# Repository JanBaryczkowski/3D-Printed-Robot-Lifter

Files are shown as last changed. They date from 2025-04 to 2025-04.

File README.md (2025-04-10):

Description: 
The lifter’s purpose is to enable the device to reach higher than the arm itself allows. Consequently, the robot operates within a broader workspace without increasing its size or modifying the arm’s construction.
The project comprises strength calculations, a 3D model of the lifter assembled with carefully selected parts and subassemblies, as well as technical drawings that predominantly consist of assembly views and a few component details. 
It also serves as part of the project assignments from the Fundamentals of Machine Construction course. The work not only demonstrates rigorous analytical and design skills but also highlights a practical approach to solving engineering
challenges while ensuring optimal functionality and structural integrity.

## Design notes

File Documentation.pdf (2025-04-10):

# Podstawy Konstrukcji Maszyn

# Projekt Podnośnika do ramienia robota wydrukowanego w 3D

## Jan Baryczkowski 152159 Mechatronika sem. V Grupa MCH1

1. Przegląd stanu techniki Podnośnik ten służy do automatycznego transportowania ramienia robota wydrukowanego w 3D wraz z przenoszonymi przez nie elementami w celu poszerzenia zakresu działania robota bez konieczności zwiększenia rozmiarów lub rozbudowy konstrukcji samego robota. Budowa tego mechanizmu nie ma zastosowania w przemyśle ze względu na małe rozmiary samego robota, ale mogłaby posłużyć jako jeden z wielu elementów Smart Home w celu np segregacji małych obiektów na różnych wysokościach za pomocą samego podnośnika wraz z

robotem.

## 2. Schemat kinematyczny

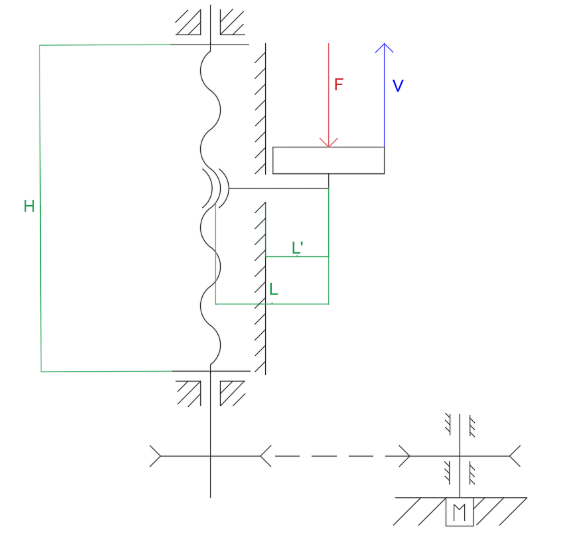
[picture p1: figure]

## 3. Dane wejściowe

## H = 400 mm - długość skoku śruby L = 45 mm- długość ramienia siły do osi śruby F = 10N - siła docisku spowodowana przez masę robota wraz z elementem przez niego przenoszonym V = 0,05 m/s - prędkość posuwu podnośnika

## 4. Spis elementów

L.p. | Nazwa | Szt. | Numer / Norma | Materiał | Uwagi
1 | Śruba trapezowa Tr 10x2 | 1 | MCH-1.00.01.0 | S215 | -
2 | Wał czynny | 1 | MCH-1.00.02.0 | C45 | -
3 | Wał bierny | 1 | MCH-1.00.03.0 | C45 | -
4 | Nakrętka trapezowa Tr 10x2 | 1 | MCH-1.00.04.0 | Brąz Bk331 | -
5 | Korpus - ściana boczna długa | 2 | MCH-1.00.05.0 | PA | -
6 | Korpus - ściana boczna krótka | 2 | MCH-1.00.06.0 | PA | -
7 | Korpus - podstawa dolna | 1 | MCH-1.00.07.0 | PA | -
8 | Korpus - podstawa górna | 1 | MCH-1.00.08.0 | PA | -
9 | Nóżka L - podstawa | 4 | MCH-1.00.09.0 | PA | -
10 | Nóżka H - podstawa | 6 | MCH-1.00.10.0 | PA | -
11 | Noga L - długa | 4 | MCH-1.00.11.0 | PA | -
12 | Noga H - długa | 6 | MCH-1.00.12.0 | PA | -
13 | Noga L - krótka | 3 | MCH-1.00.13.0 | PA | -
14 | Noga H - krótka | 4 | MCH-1.00.14.0 | PA | -
15 | Oprawa łożyska 1 | 2 | MCH-1.00.15.0 | PA | -
16 | Oprawa łożyska 2 | 2 | MCH-1.00.16.0 | PA | -
17 | Korpus - piętro | 2 | MCH-1.00.17.0 | PA | -
18 | Korpus - belka wąska | 1 | MCH-1.00.18.0 | PA | -
19 | Korpus - belka szeroka | 1 | MCH-1.00.19.0 | PA | -
20 | Kątownik | 2 | MCH-1.00.20.0 | PA | -
21 | Wieża - podpora | 1 | MCH-1.00.21.0 | PA | -
22 | Wieża - ściana boczna krótka | 1 | MCH-1.00.22.0 | PA | -
23 | Wieża - ściana boczna długa | 1 | MCH-1.00.23.0 | PA | -
24 | Wieża - podstawa dolna | 1 | MCH-1.00.24.0 | PA | -
25 | Wieża - podstawa środkowa | 1 | MCH-1.00.25.0 | PA | -
26 | Wieża - pokrycie | 1 | MCH-1.00.26.0 | PA | -
27 | Wieża - usadowienie robota | 1 | MCH-1.00.27.0 | PA | -
28 | Wieża - noga L | 4 | MCH-1.00.28.0 | PA | -
29 | Sprzęgło | 2 | WKE_N-9-5-5-98 | - | -
30 | Wózek prowadnicy | 2 | Katalog HIWIN | - | -
31 | Szyna prowadnicy MGNR07R500HMI | 2 | Katalog HIWIN | - | -
32 | Silnik | 1 | IW-S-000-008 | - | -
33 | Wpust pryzmatyczny 21x3x3 | 4 | PN-85002 | C45 | -
34 | Wpust pryzmatyczny 21x4x4 | 1 | PN-85002 | C45 | -
35 | Pas zębaty | 1 | PN-83/M-85210 | - | -
36 | Łożysko poprzeczne 618/8 | 2 | Katalog SKF | - | -
37 | Łożysko wzdłużne BA8 | 1 | Katalog SKF | - | -
38 | Koło napędowe | 1 | PN-84/M-85211 | PA | -
39 | Koło napędzane | 1 | PN-84/M-85211 | PA | -

40 | Segger Z8 | 10 | ANSI B 27.7M -3AMI-9 | - | -
41 | Segger Z10 | 1 | ANSI B 27.7M -3AMI-11 | - | -
42 | Śruba M4 x 35 | 2 | ISO 1580 | - | -
43 | Śruba M4 x 25 | 8 | ISO 1580 | - | -
44 | Śruba M4 x 10 | 26 | ISO 1580 | - | -
45 | Nakrętka M4 | 53 | ISO 4032 | - | -
46 | Nakrętka M4 BS | 8 | BS EN 24 036 | - | -
47 | Podkładka płaska AS | 8 | AS 1237 - 4 | - | -
48 | Podkładka sprężysta M4 Typ B | 117 | BS 4464 | - | -
49 | Podkładka płaska | 168 | ISO 7089 - 4 | - | -
50 | Śruba M4x14 | 20 | ISO 1580 | - | -
51 | Śruba M4 x 20 | 31 | ISO 1580 | - | -
52 | Śruba trzpieniowa M1,6 x 6 | 8 | ISO 4766 | - | -
53 | Nakrętka M4 4183 | 24 | BS 4183 | - | -
54 | Śruba M4 x 16 | 6 | ISO 1580 | - | -
55 | Śruba M4 x 12 | 4 | ISO 1580 | - | -
56 | Śruba M4 x 40 | 4 | ISO 1580 | - | -
57 | Śruba M4 x 30 | 3 | ISO 1580 | - | -
58 | Podkładka płaska M2,5 | 8 | ISO 7089 | - | -
59 | Podkładka sprężysta M2,5 Typ B | 8 | BS 4464 | - | -
60 | Śruba M2,5 x 16 | 4 | ISO 1580 | - | -
61 | Nakrętka M2,5 | 4 | BS 4183 - M2,5 | - | -

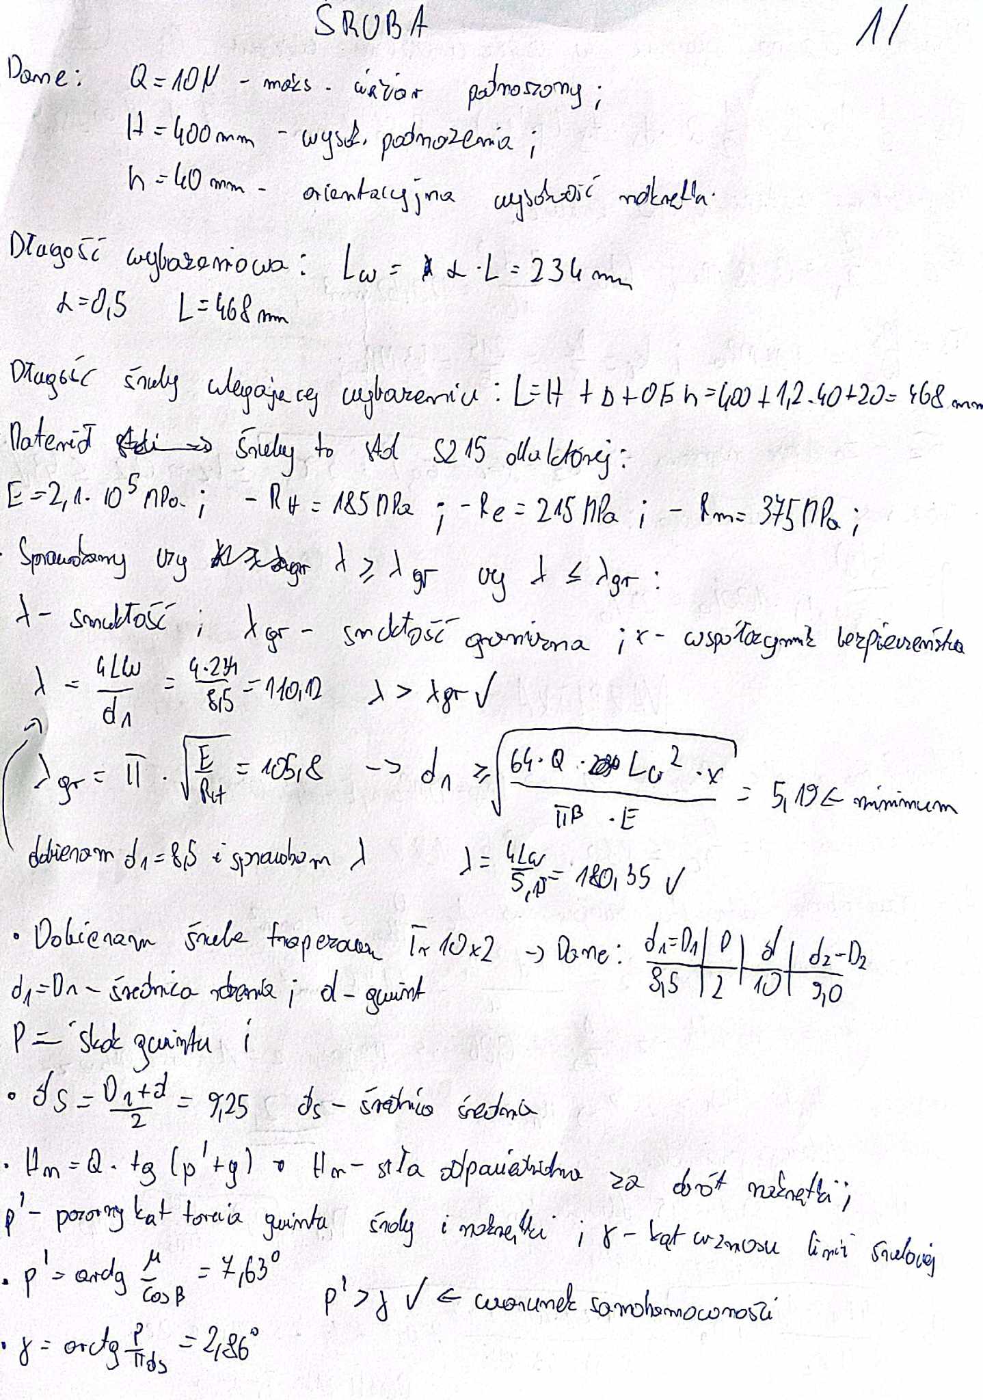
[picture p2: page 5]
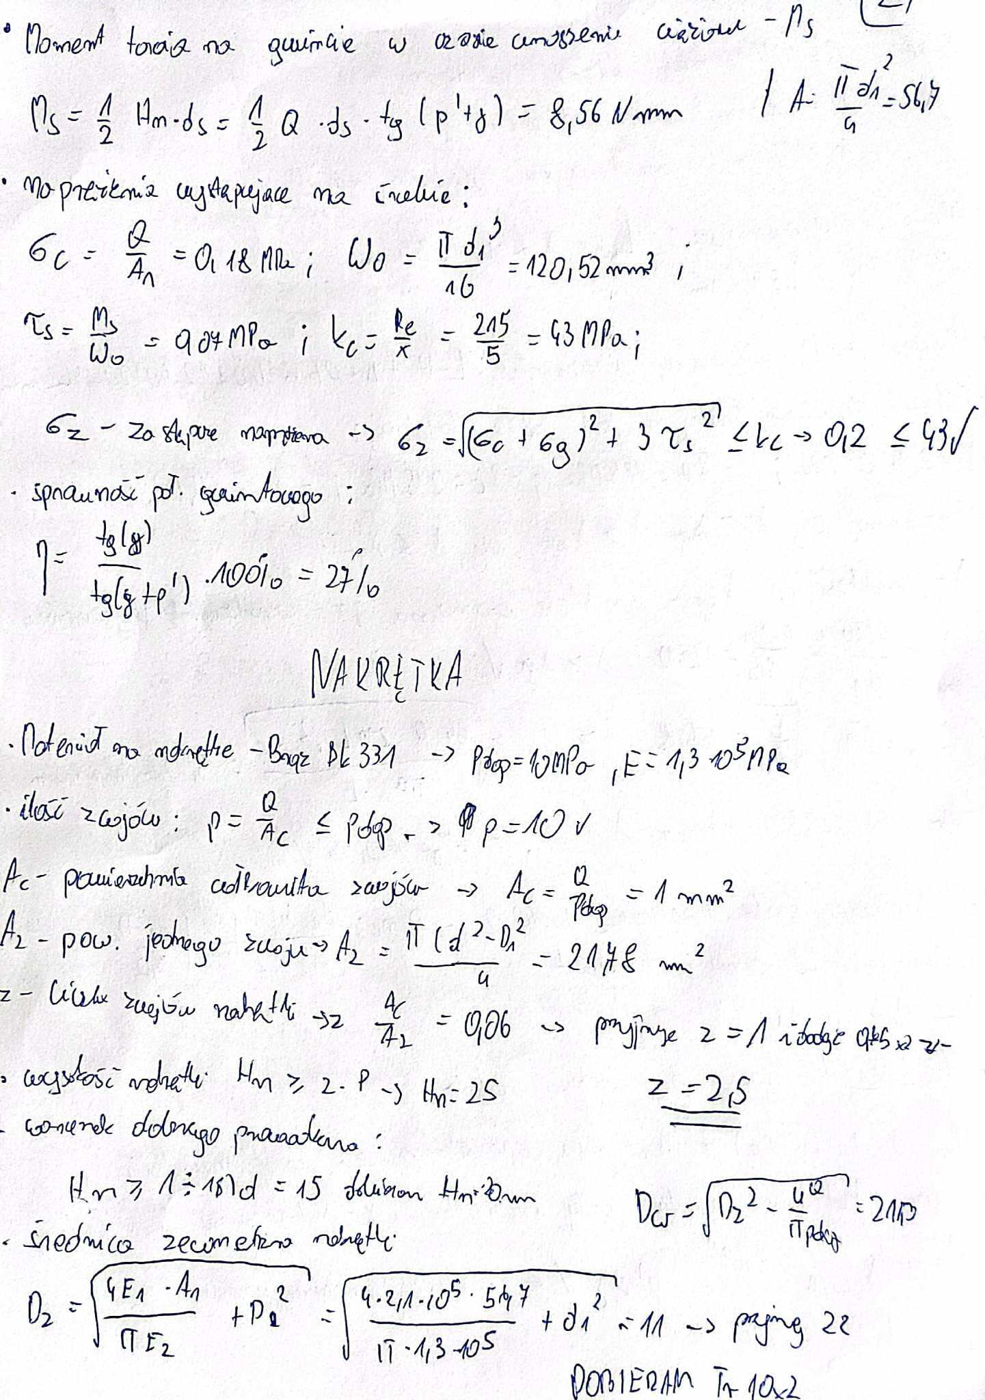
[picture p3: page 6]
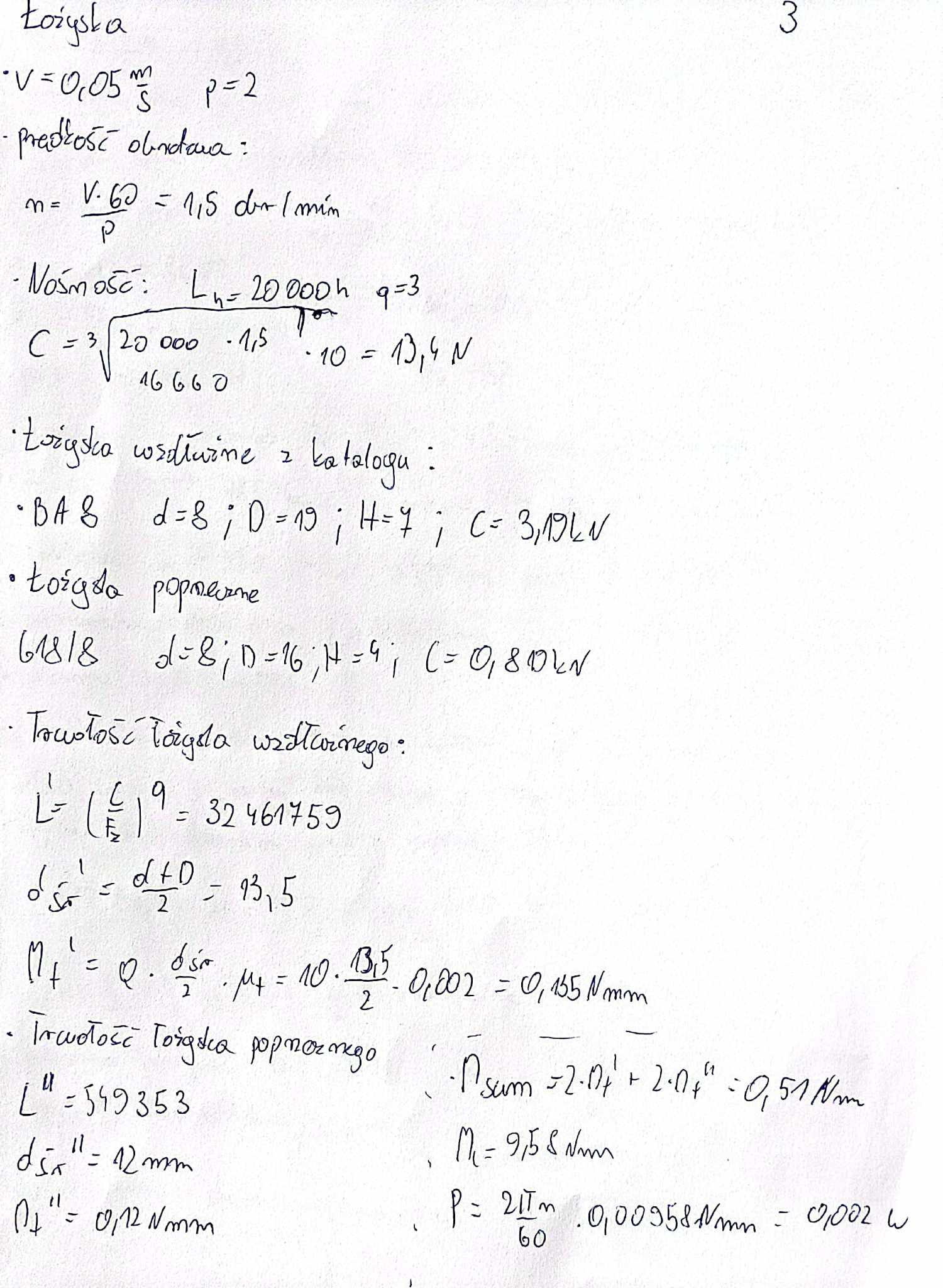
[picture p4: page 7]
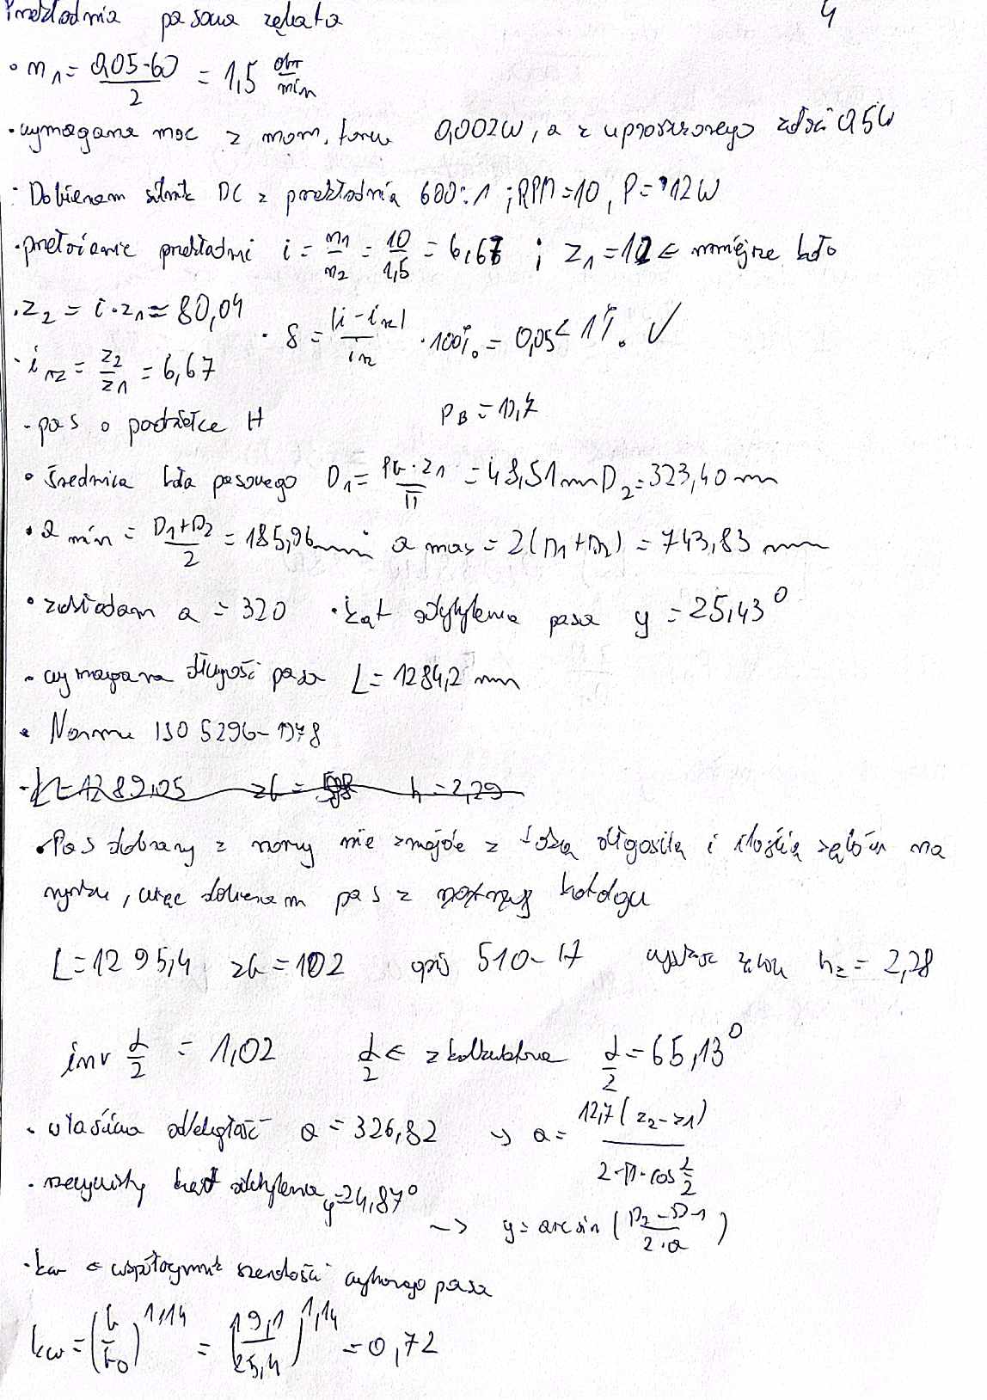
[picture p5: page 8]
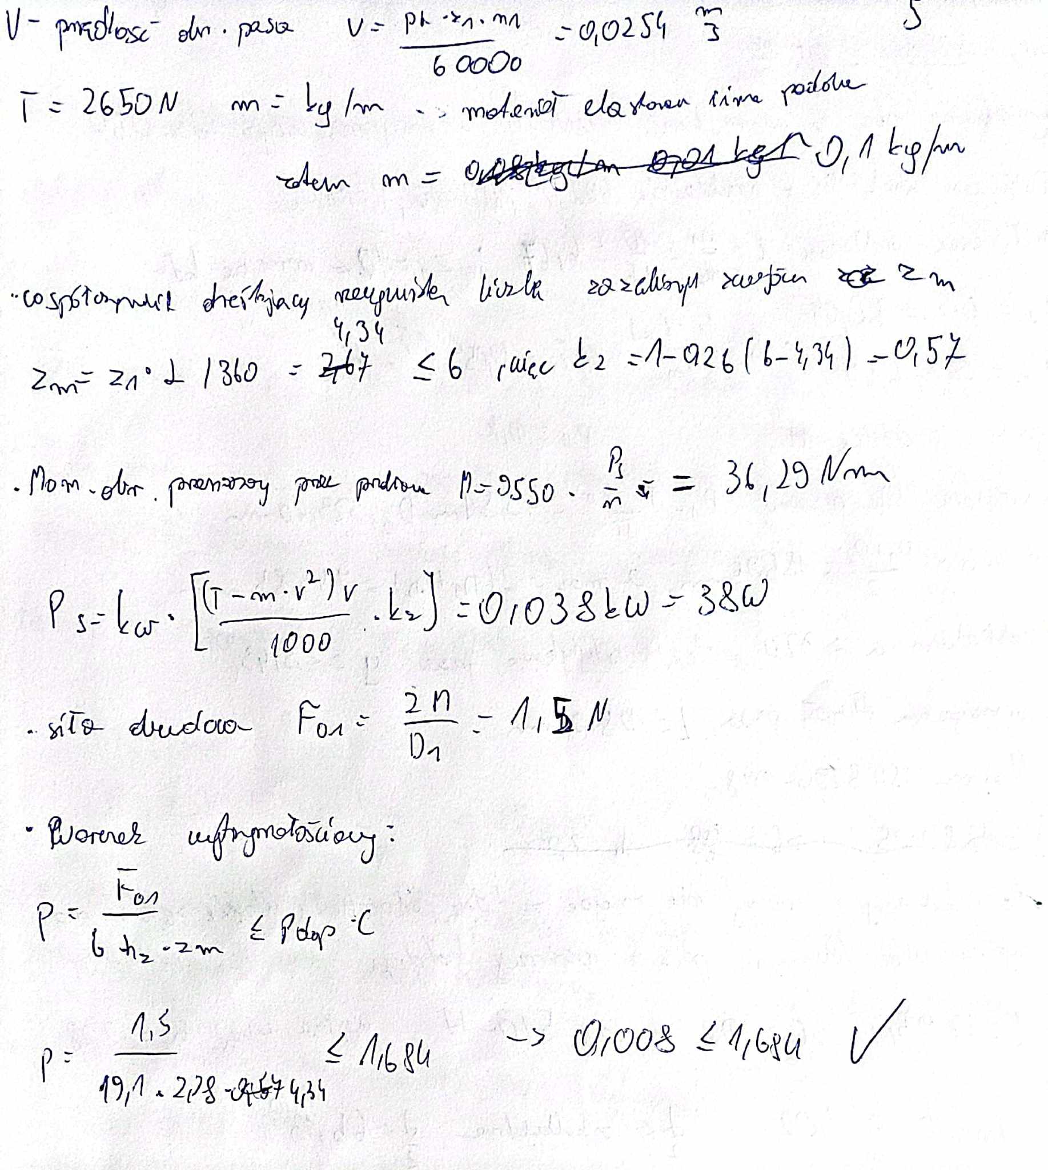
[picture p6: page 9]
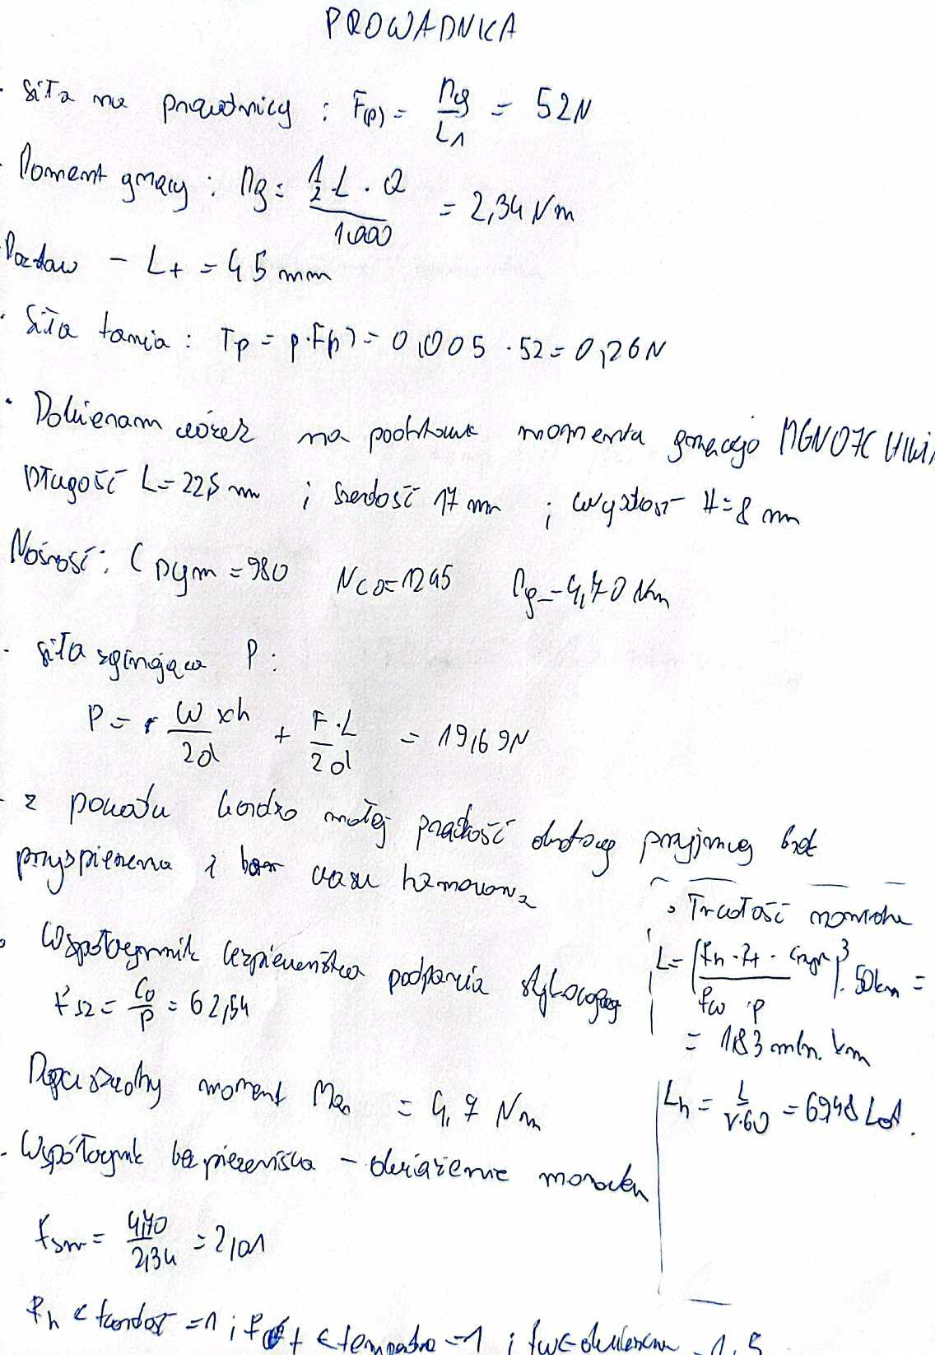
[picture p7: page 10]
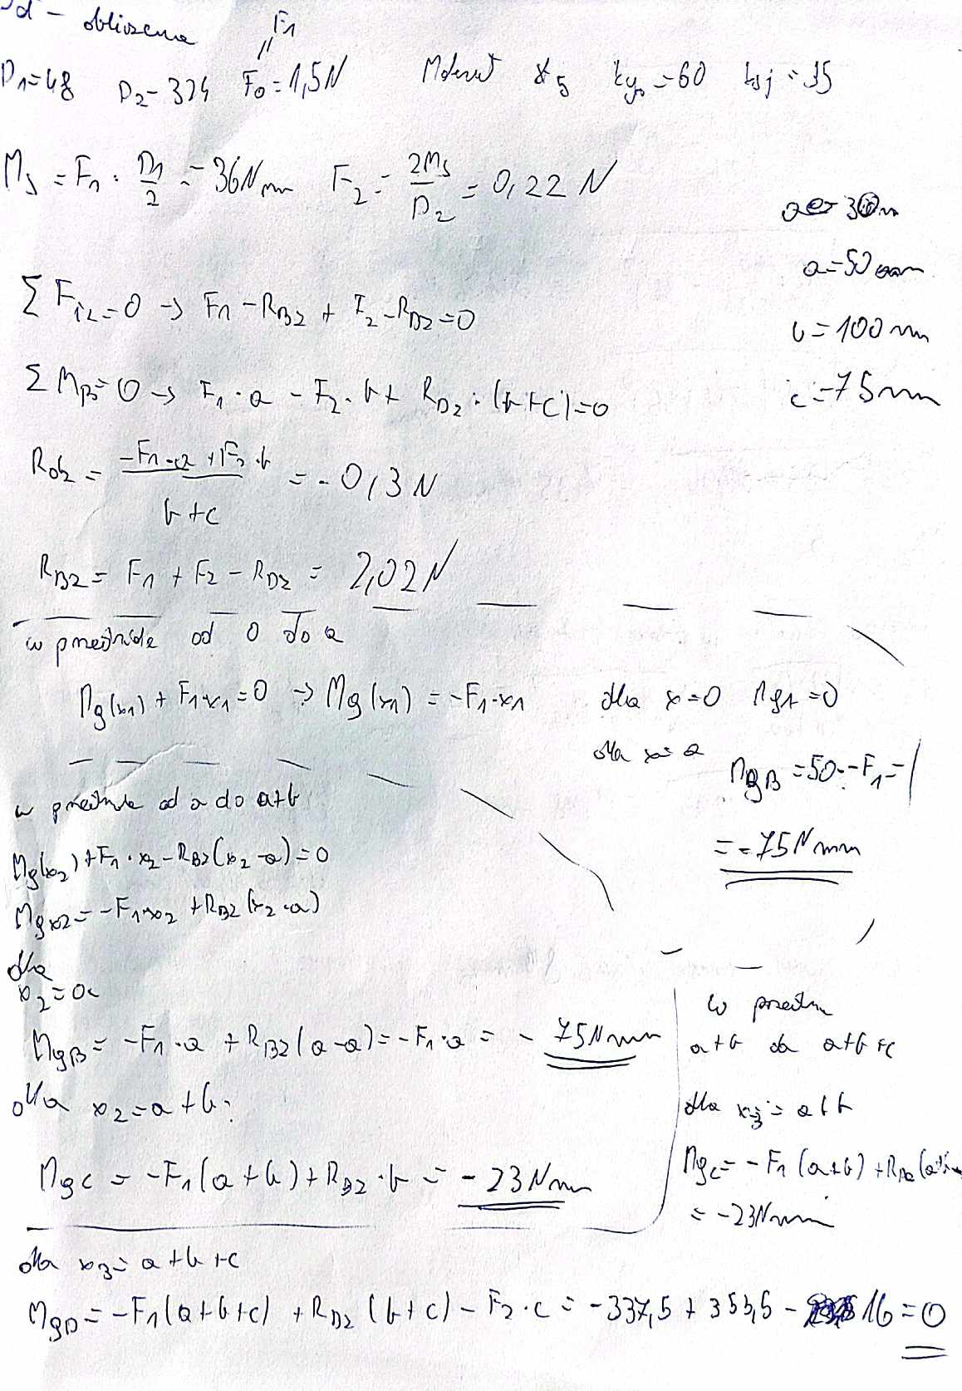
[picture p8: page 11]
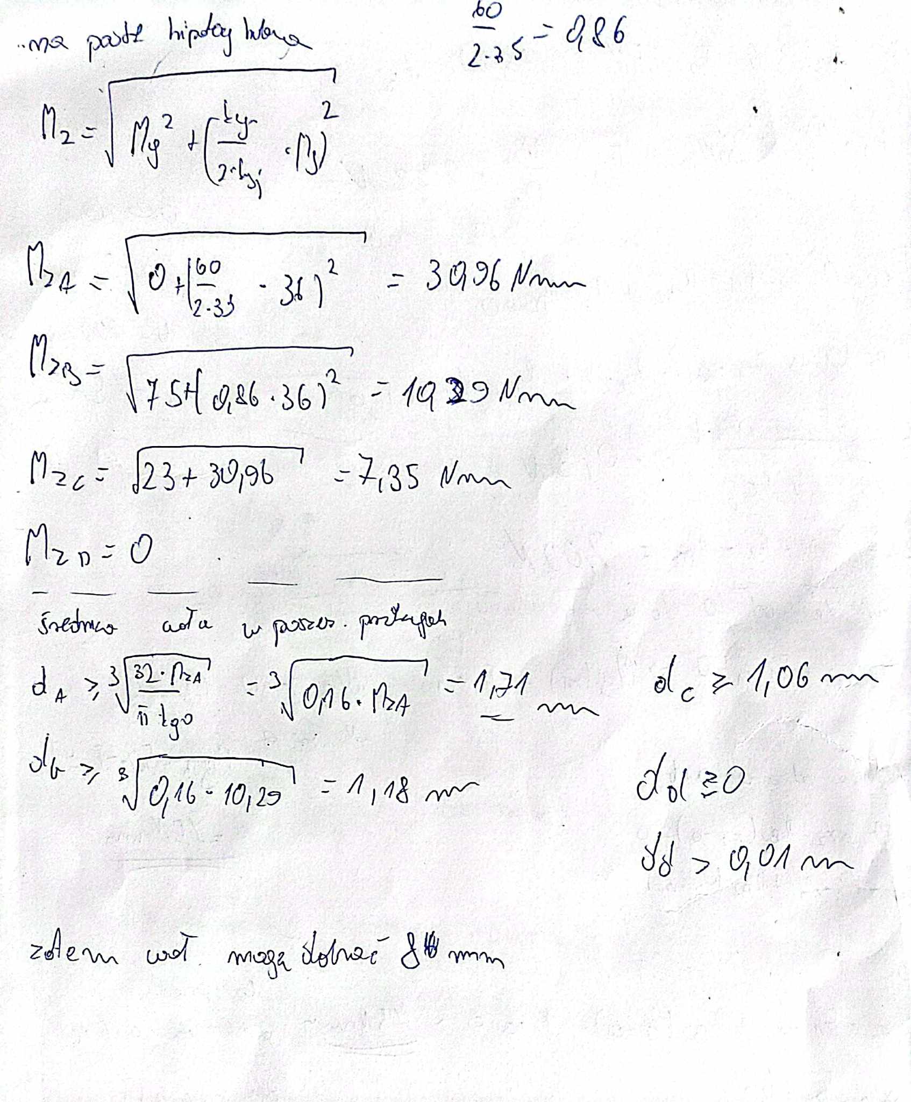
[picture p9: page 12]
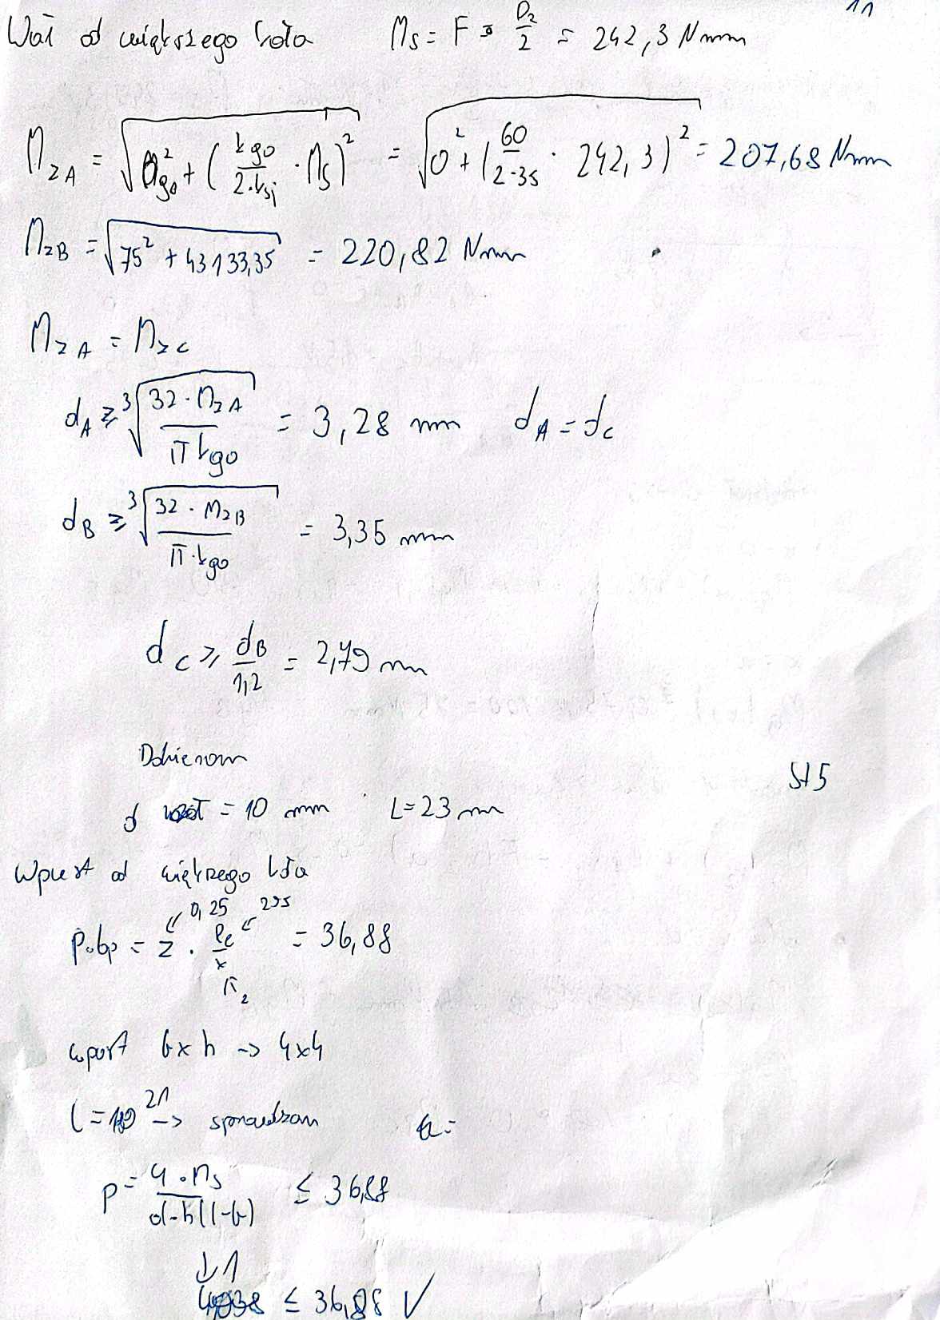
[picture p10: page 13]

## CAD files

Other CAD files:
Drawings/Jan Baryczkowski - rysunki.dwg

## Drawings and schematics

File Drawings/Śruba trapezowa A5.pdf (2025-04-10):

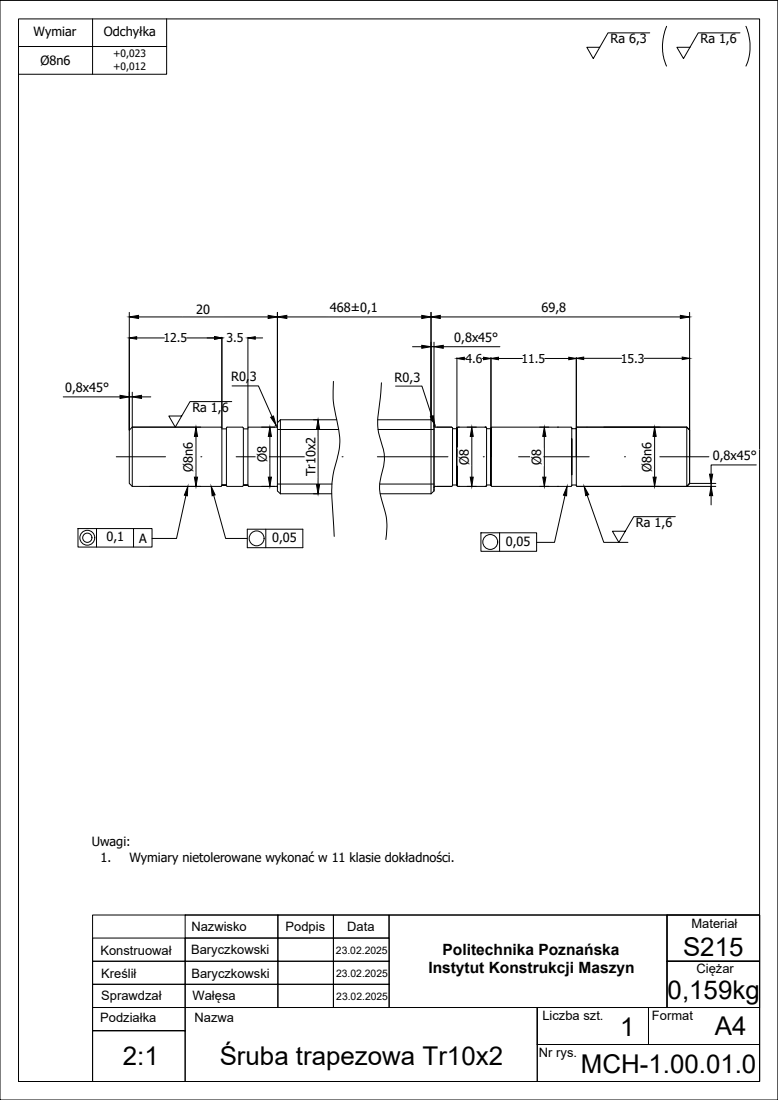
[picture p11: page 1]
Śruba trapezowa Tr10x2; Nazwa; Liczba szt.; Format; Nr rys.

Wymiar | Odchyłka

Uwagi:
1. Wymiary nietolerowane wykonać w 11 klasie dokładności.

Nazwisko | Podpis | Data | Politechnika Poznańska Instytut Konstrukcji Maszyn | Materiał S215

Konstruował | Baryczkowski | | 23.02.2025
Kreślił | Baryczkowski | | 23.02.2025 | | Ciężar 0,159kg

Sprawdzał | Wałęsa | | 23.02.2025

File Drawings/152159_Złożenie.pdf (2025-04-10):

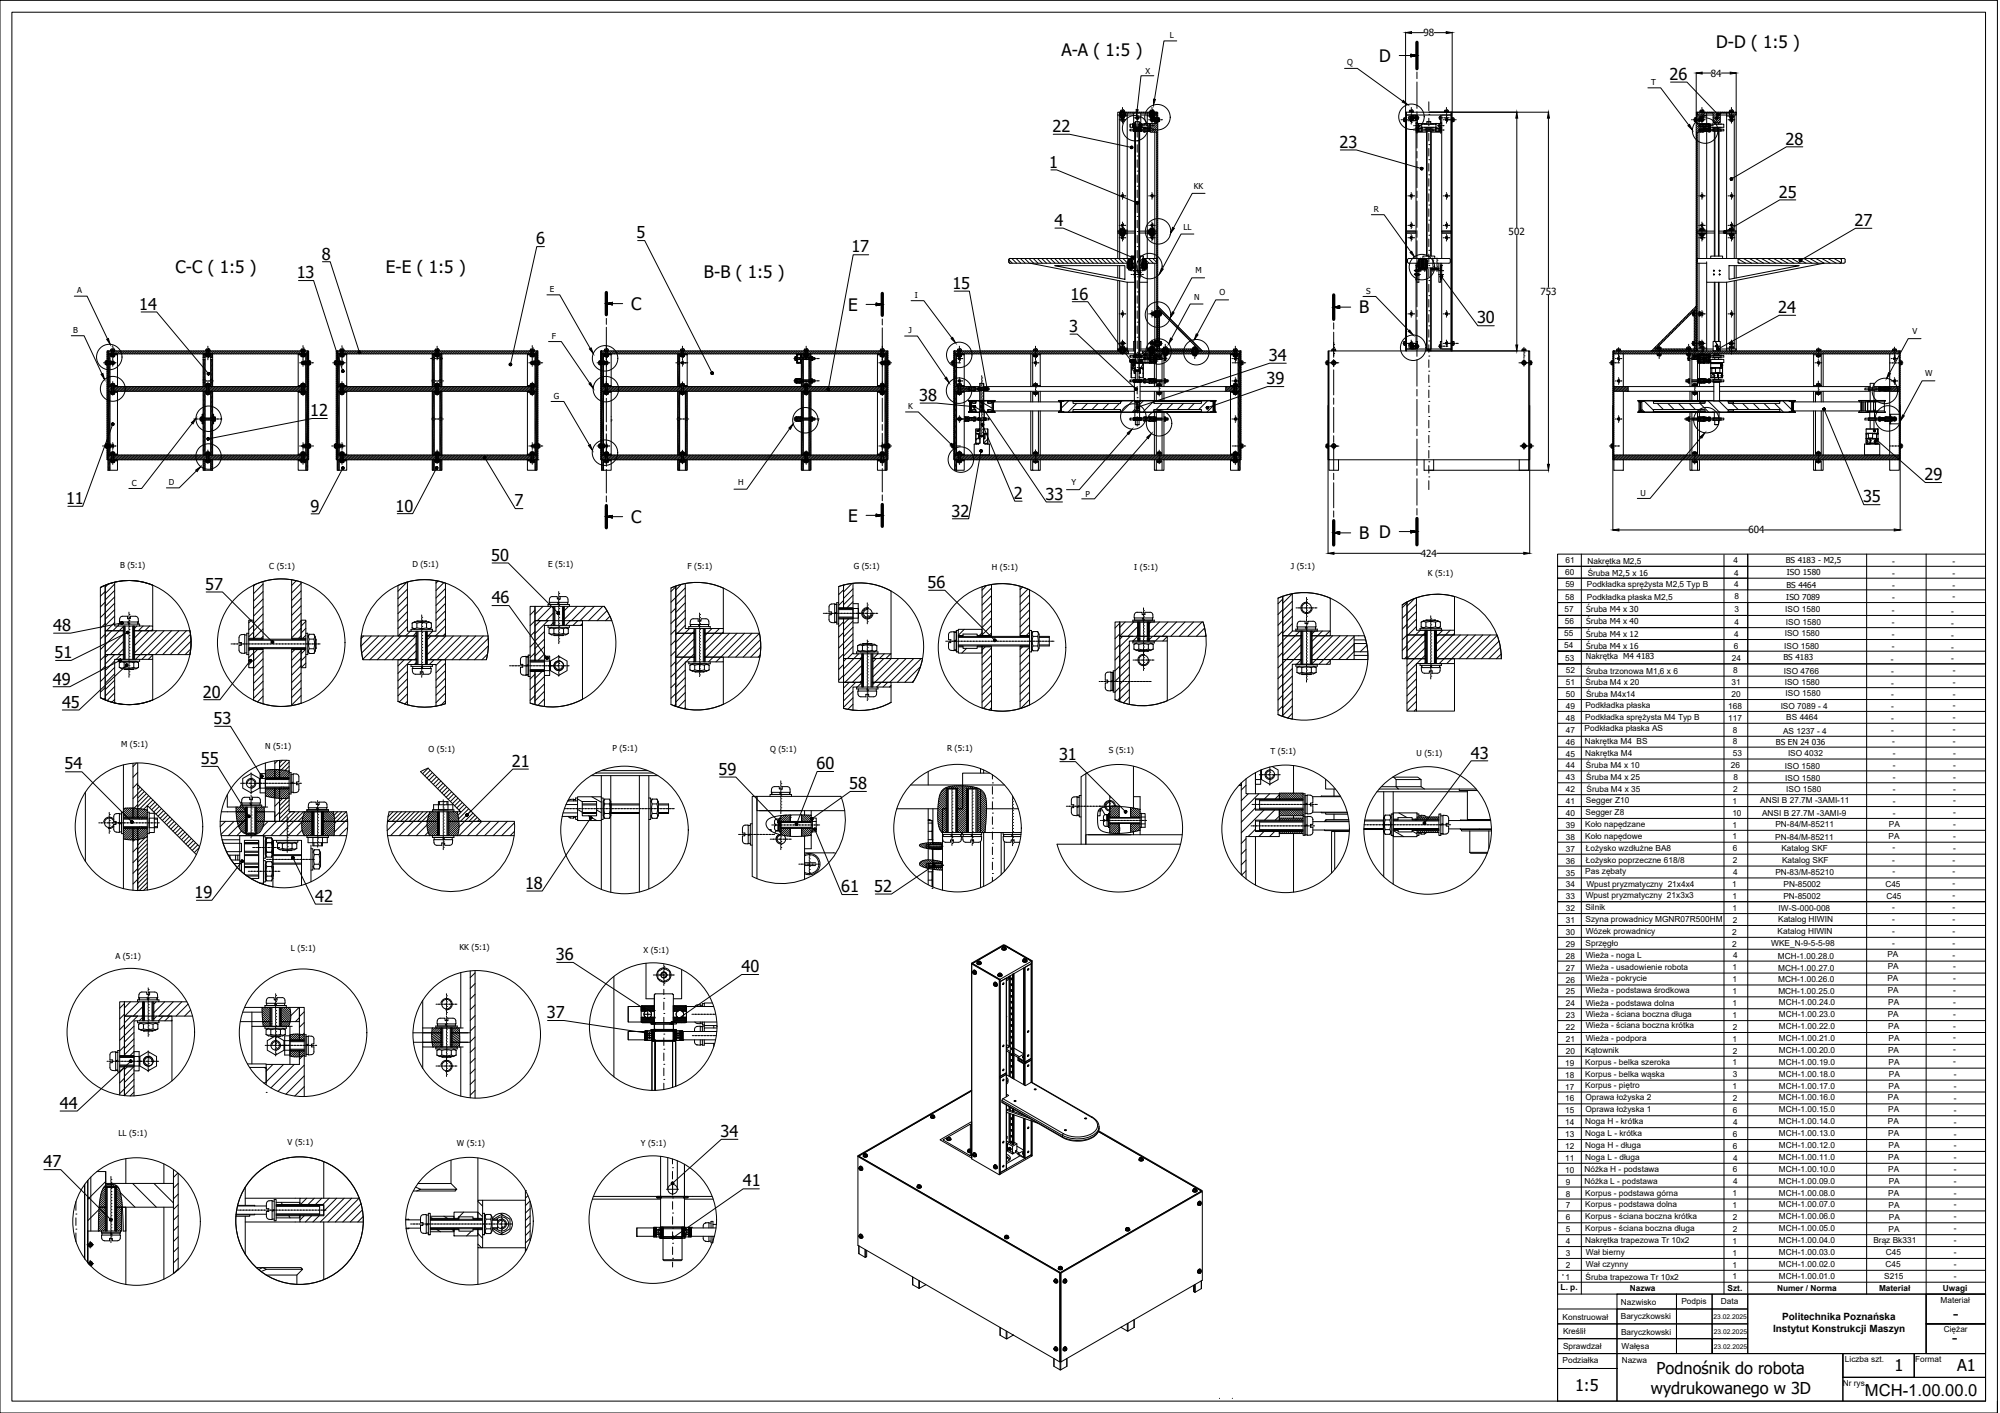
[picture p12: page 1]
EFG; wydrukowanego w 3D; Noga H - długa Noga L - długa Nóżka H - podstawa Nóżka L - podstawa; Korpus - podstawa dolna; Korpus - ściana boczna krótka Korpus - ściana boczna długa Nakrętka trapezowa Tr 10x2 Wał bierny Wał czynny Śruba trapezowa Tr 10x2; Nakrętka M4; Segger Z8 Koło napędzane Koło napędowe Łożysko wzdłużne BA8 Łożysko poprzeczne 618/8 Pas zębaty; Wpust pryzmatyczny 21x3x3; Szyna prowadnicy MGNR07R500HM Wózek prowadnicy; Wieża - noga L Wieża - usadowienie robota Wieża - pokrycie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

Korpus - podstawa górna

Politechnika Poznańska
Instytut Konstrukcji Maszyn

Baryczkowski
Wałęsa
Podnośnik do robota

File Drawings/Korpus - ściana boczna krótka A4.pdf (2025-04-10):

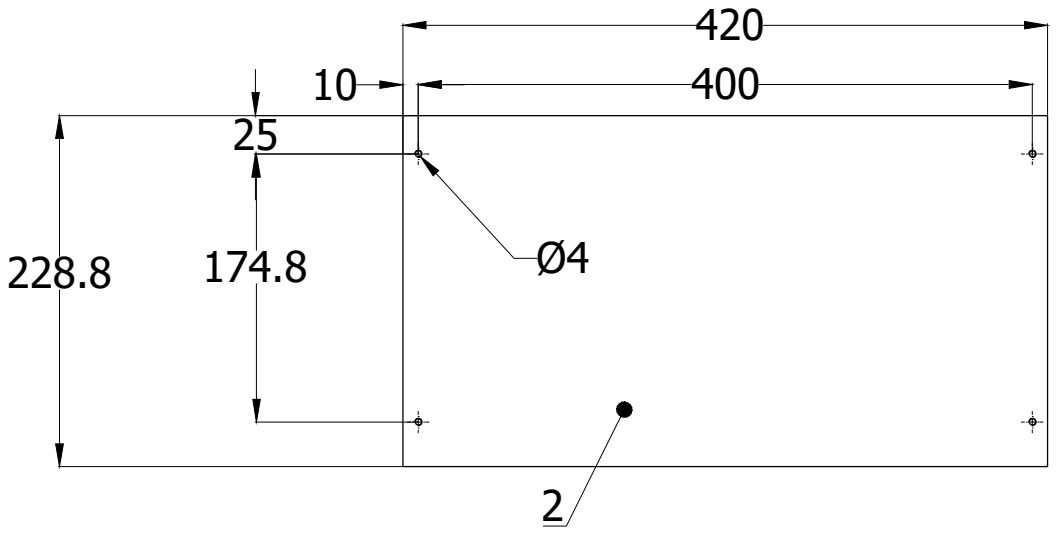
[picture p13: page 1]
Korpus - ściana boczna krótka; MCH-1.00.06.0; Nr rys.

Nazwisko | Podpis | Data | Politechnika Poznańska Instytut Konstrukcji Maszyn | Materiał PA

Konstruował | Baryczkowski | | 23.02.2025
Kreślił | Baryczkowski | | 23.02.2025 | | Ciężar

Sprawdzał | Wałęsa | | 23.02.2025
Podziałka | Nazwa | Liczba szt. | Format

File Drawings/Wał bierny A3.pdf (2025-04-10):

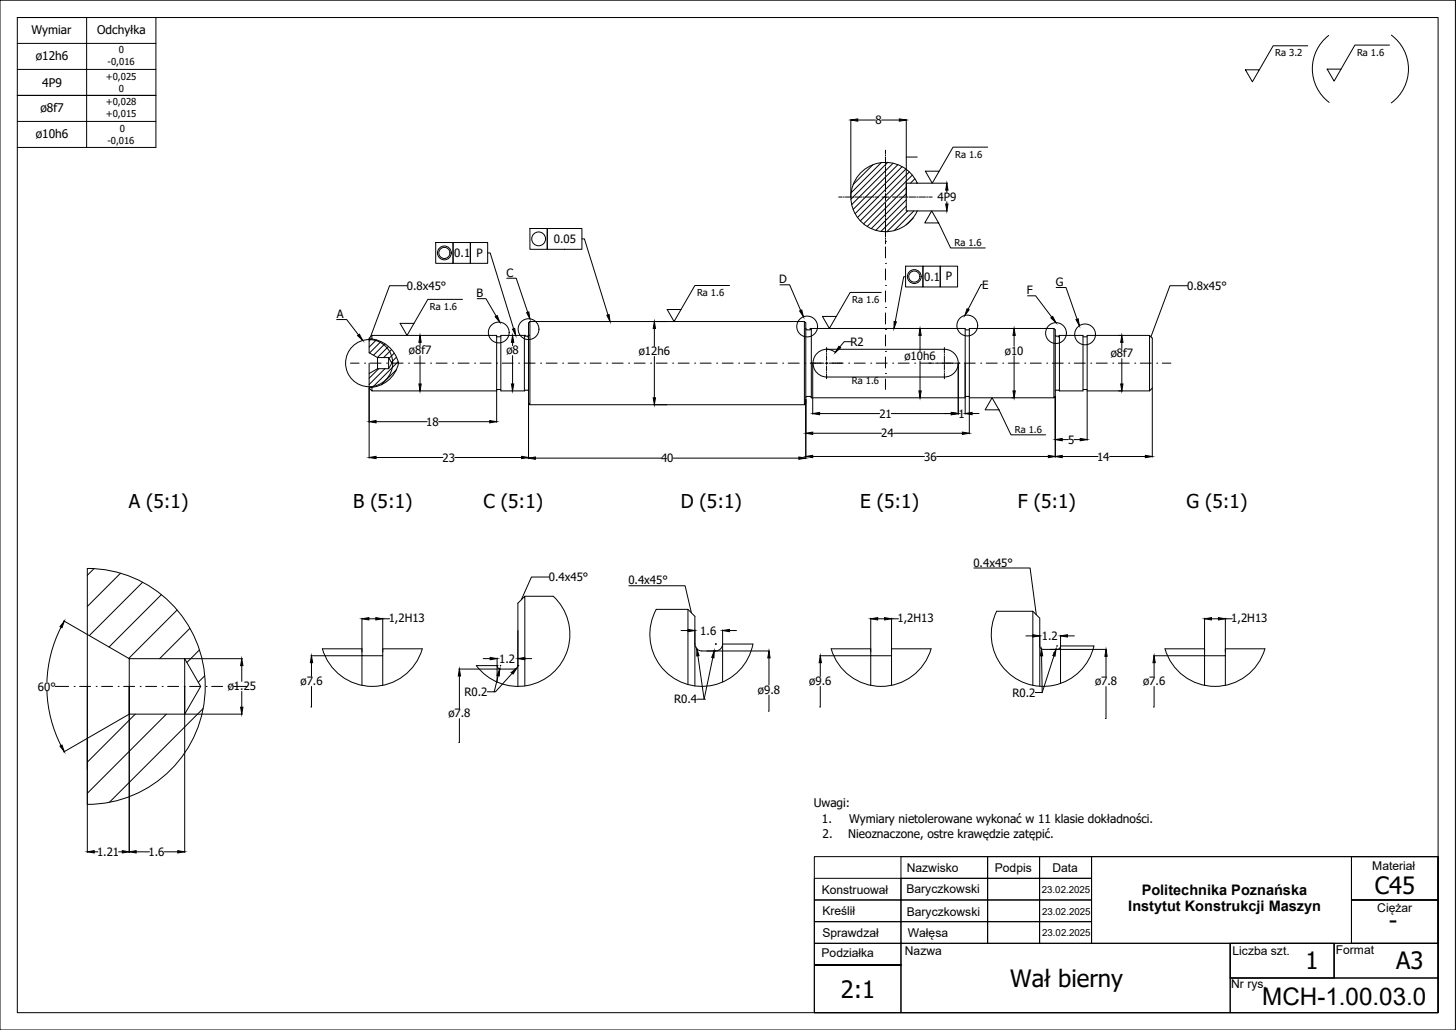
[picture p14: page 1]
Wał bierny; MCH-1.00.03.0; Nr rys.

Wymiar | Odchyłka
ø12h6 | 0 -0,016

Uwagi:
1. Wymiary nietolerowane wykonać w 11 klasie dokładności.
2. Nieoznaczone, ostre krawędzie zatępić.

Nazwisko | Podpis | Data | Politechnika Poznańska Instytut Konstrukcji Maszyn | Materiał C45

Konstruował | Baryczkowski | | 23.02.2025
Kreślił | Baryczkowski | | 23.02.2025 | | Ciężar

Sprawdzał | Wałęsa | | 23.02.2025
Podziałka | Nazwa | Liczba szt. | Format

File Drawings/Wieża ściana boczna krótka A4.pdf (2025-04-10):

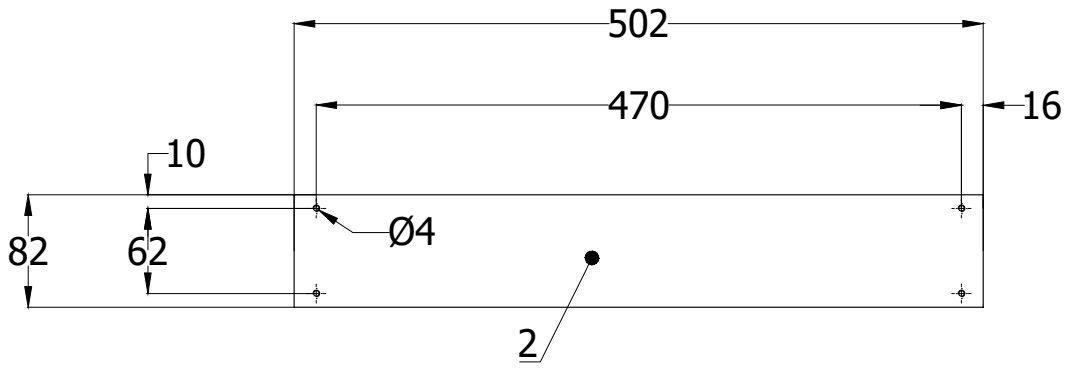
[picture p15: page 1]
MCH-1.00.22.0; Nr rys.

Nazwisko | Podpis | Data | Politechnika Poznańska Instytut Konstrukcji Maszyn | Materiał PA

Konstruował | Baryczkowski | | 23.02.2025
Kreślił | Baryczkowski | | 23.02.2025 | | Ciężar
Podziałka | Nazwa Wieża - ściana boczna krótka | Liczba szt. 2 | Format A4

Sprawdzał | Wałęsa | | 23.02.2025
